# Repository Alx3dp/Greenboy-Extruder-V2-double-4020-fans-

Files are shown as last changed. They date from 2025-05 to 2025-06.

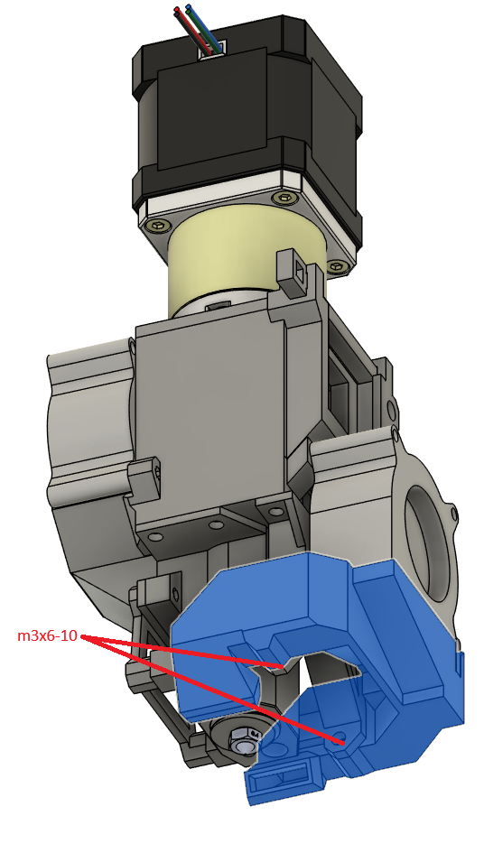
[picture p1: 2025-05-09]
Pellet printhead V2/assembly guide/step_9.png

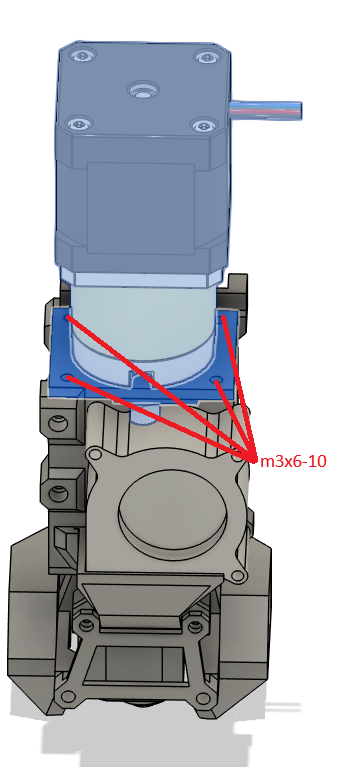
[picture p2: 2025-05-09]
Pellet printhead V2/assembly guide/step_11.png

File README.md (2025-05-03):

This is an alternate printhead for the Greenboy3d Pellet Extruder 
<br>
The goal of this project is to offer an alternate printhead to the original one with a multitude of improvements whith minimal extra parts needed over the kit the extruder comes with.
<br>
Notable improvements are:
<br>
<br>
A removable connector for the pellet hose including a gate to stop the pellet flow.
<br>
A significant improvement of the location of the center of mass(COM) of the printhead to hopefully allow faster printing
<br>
A mounting plate seperate of the main body which makes it significantly easier to create custom mounts and makes it possible to remove the printhead from the printer with minimal disassembly
<br>
Hopefully improved cooling
<br>
It is more compact than the original printhead
<br>
A dedicated mount for a multitude of z probes (still a wip)
<br>
There are also 2 versions, one with the pellet hose on the left and one with it on the right
<br>
<br>
Do keep in mind that this is still a wip. there can be issues, I can make mistakes and my designs are not perfect. If you find an issue or have any Ideas on how to improve this design please message me on discord @alx1234
<br>
You will need additional parts to the GB kit, consult the BOM to see what exactly you will need.
<br>
As the motor is by far the heaviest part of the printhead, the COM is located relatively high up. The closer the COM is to the x axis the better it is.
<br>
As a consequence of that the printhead has been moved down compared to the original, meaning you will lose a few centimeters of z travel.
<br>
<br>
The Fans I use as reference are a different model as the ones included with the GB kit, so they do not lign up with the fixtures in the .step files.
<br>
<br>
You need to ause support when printing these parts, I would recommend just using your standard tree support.
<br>
<br>
The main body of the printhead is in direct contact with the extruder barrel, so pla is most likely not sufficient for this part. So use something with better heat resistance like petg or abs at least for that part.

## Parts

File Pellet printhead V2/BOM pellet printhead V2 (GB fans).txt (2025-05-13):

The screw set included with the Greenboy pellet Extruder contains the 2 m3x25 and m3x18 screws that are needed for the fans,
as well as 12 m3x10 screws. 

So you need to source the rest of the screws yourself

Fans: 			2x m3x18			#for hotend cooling fan
			2x m3x18-25			#for part cooling fan

Motor mount:		4x m3x5x4 heat set insert	#located on top of the main body
			4x m3x8-12				#to secure the motor to the motor plate
			4x m3x6 to m3x10		#to secure the motor plate to the main body

Mounting plate:		4x m3x5x4 heat set insert	#for all Version, located on the side of the main body
			4x m3x6 to m3x10  		#for all Version
			4x m3x6				#for xol carriage
			2x m3x6 to m3x10		#for Ender 3
			2x m3x5 to m3x12		#for Neptune 3, the original Filament printhead uses 2 m3x8 for this 

hotend cooling duct:	2x m3x6 to m3x10		#to secure the fixture to the main Body
			
Z probe fixture:	4x m3x16 			#for cartographer probe
			2x m3x6				#for cartographer probe
			4x m3x10 to m3x12 		#for no probe

Part cooling duct:	2x m3x6 to m3x10		#to secure the fixture to the main Body,
			2x m3x6 to m3x10		#to secure the duct to the fixture

Extruder Barrel:	4 m4x8 to m4x12			#to secure the extruder barrel to the main body

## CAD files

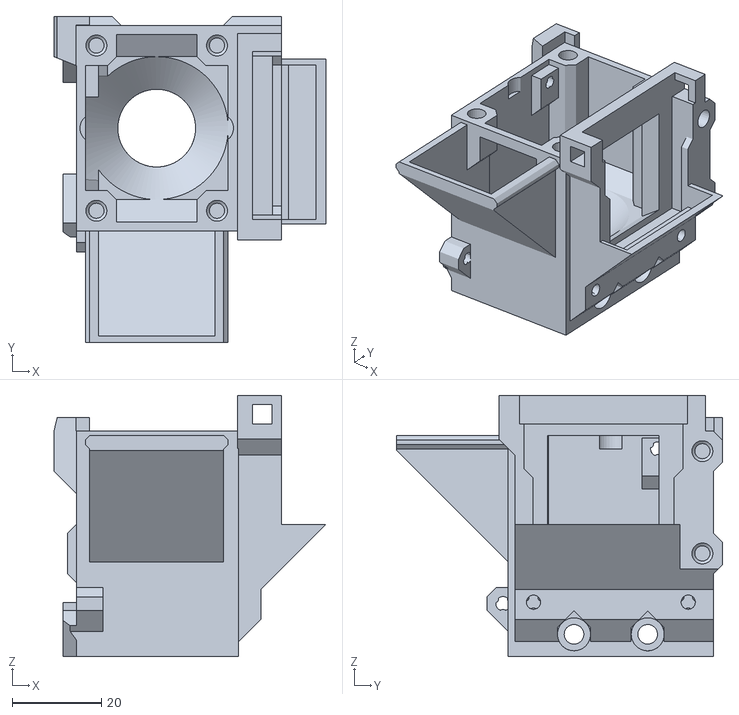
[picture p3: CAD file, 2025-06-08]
Pellet printhead V2/general/body designs/main body bucket.stl
60.9 x 73.0 x 58.5

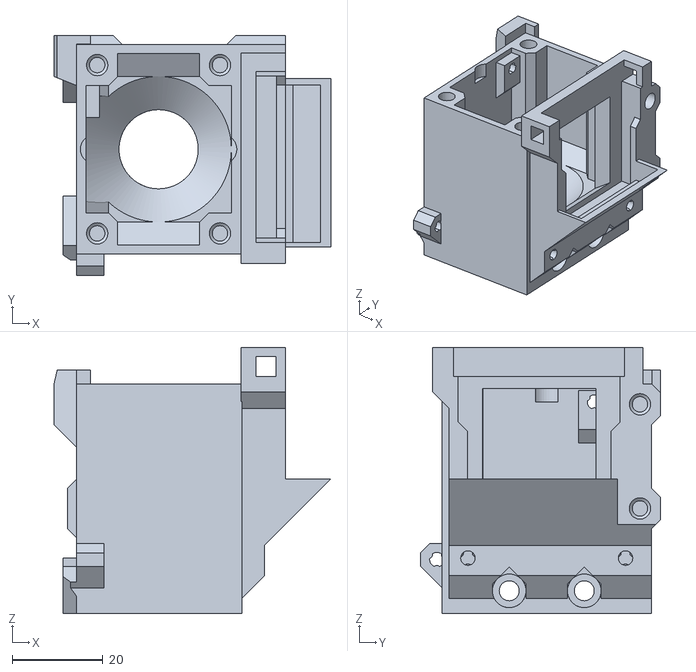
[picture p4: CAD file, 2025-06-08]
Pellet printhead V2/general/body designs/main body normal.stl
60.9 x 52.7 x 58.5

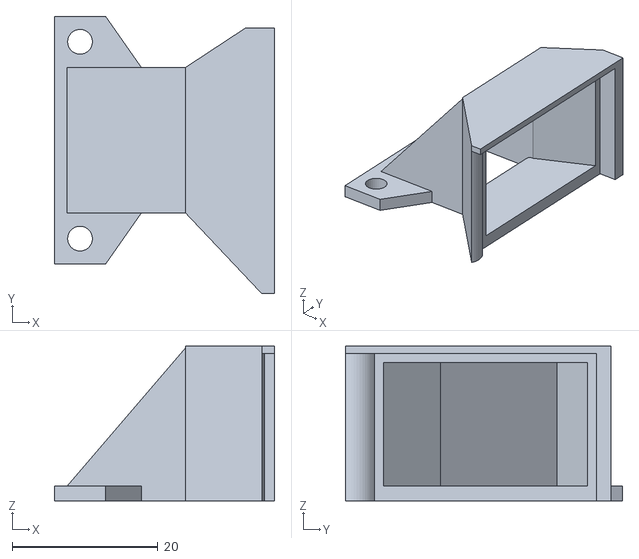
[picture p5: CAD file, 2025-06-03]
Pellet printhead V2/general/hotend fan duct.stl
30.2 x 38.1 x 21.2

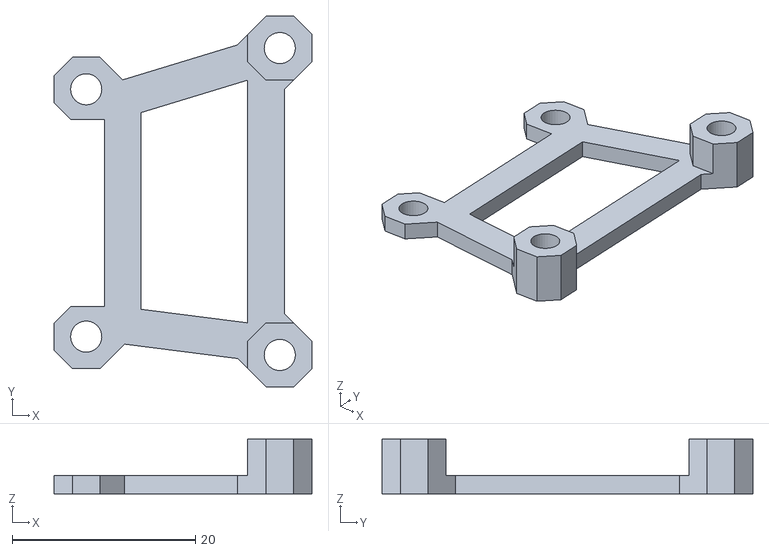
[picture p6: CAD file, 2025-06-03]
Pellet printhead V2/general/z probe adapters/no Z probe fixture.stl
28.1 x 40.5 x 6.00

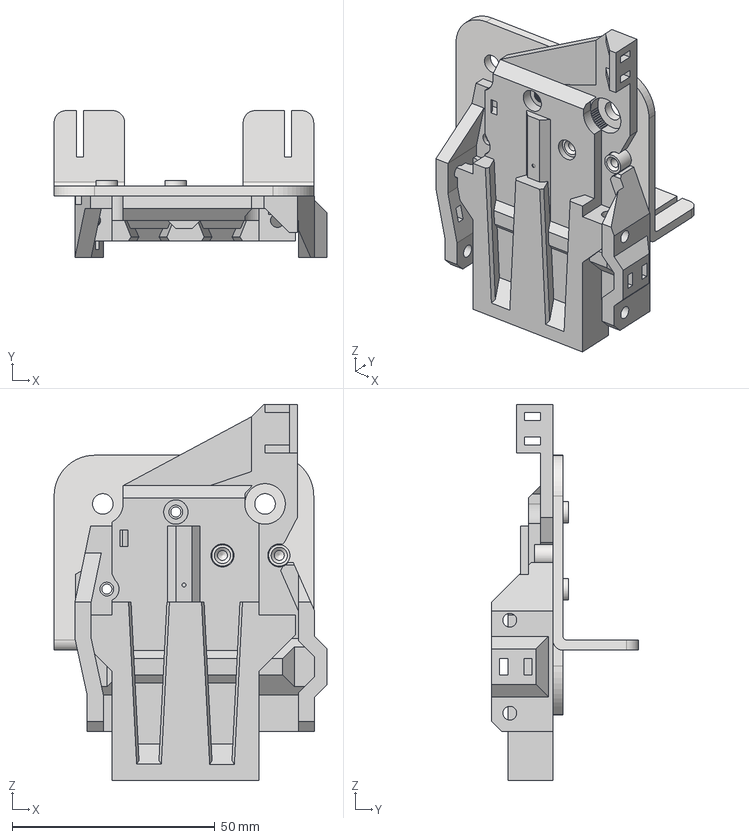
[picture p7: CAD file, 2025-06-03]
Pellet printhead V2/Mounting plates/Ender3/Ender3 pro mounting plate cad.step
67.2 x 36.2 x 92.7 mm
Основание_3
Pellet printhead V2 (GB parts) pellet hose right
Pellet printhead V2 (GB parts) pellet hose right_1

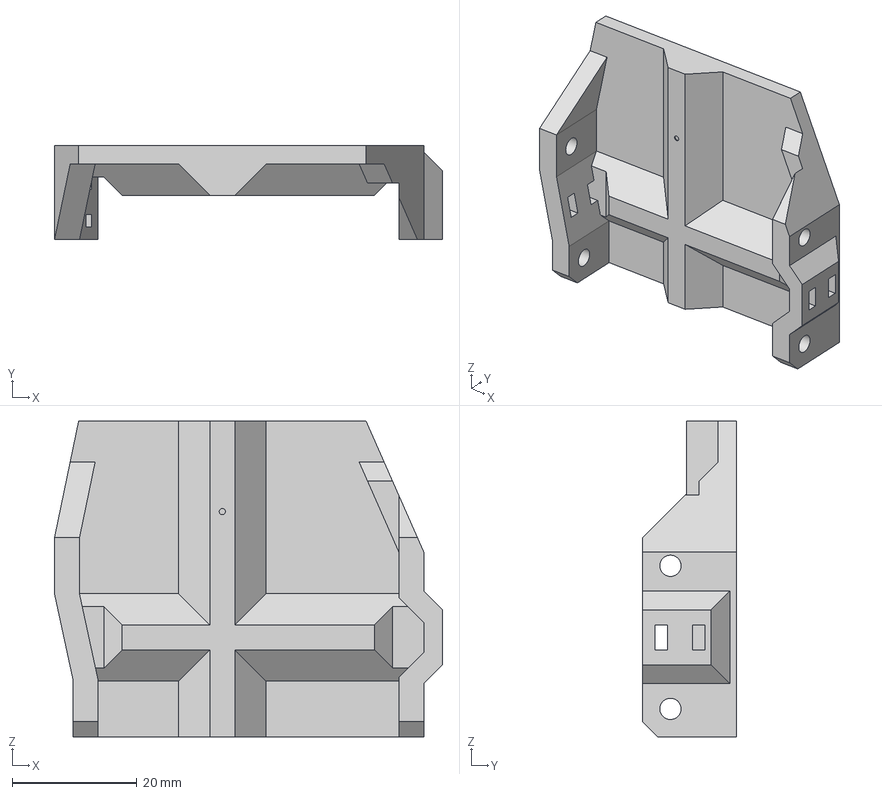
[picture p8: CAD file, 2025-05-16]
Pellet printhead V2/Mounting plates/mounting plate base hose right.step
62.1 x 15.1 x 50.6 mm

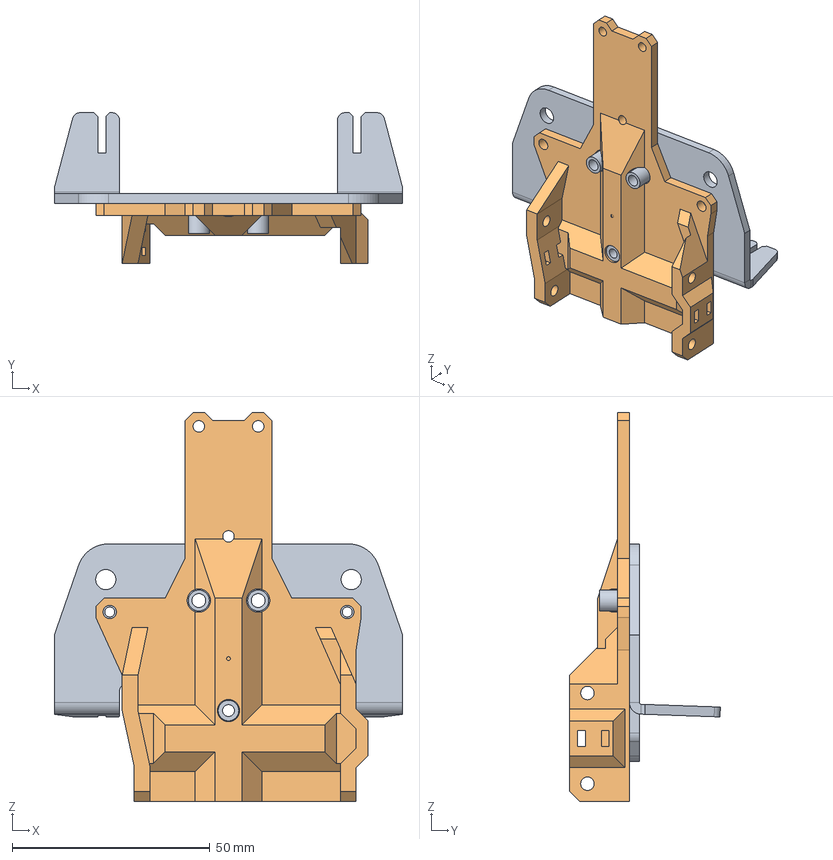
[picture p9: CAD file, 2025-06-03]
Pellet printhead V2/Mounting plates/Neptune 3/Neptune 3 Pro mounting plate cad.step
88.0 x 38.1 x 98.3 mm
FIXING_PLATE_EXTRUDER
Pellet printhead V2 (GB parts) pellet hose right

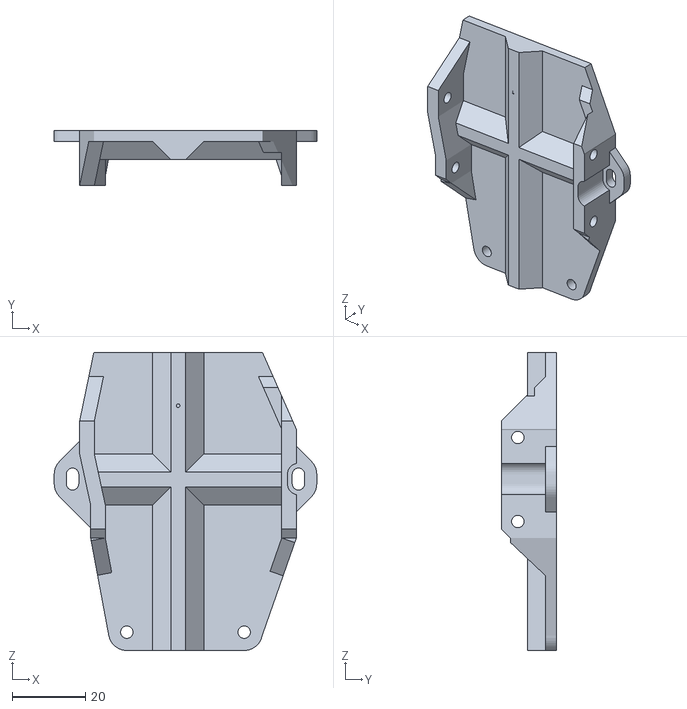
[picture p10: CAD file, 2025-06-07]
Pellet printhead V2/Mounting plates/Orange storm giga/orange storm giga mounting plate.stl
71.6 x 15.1 x 81.2

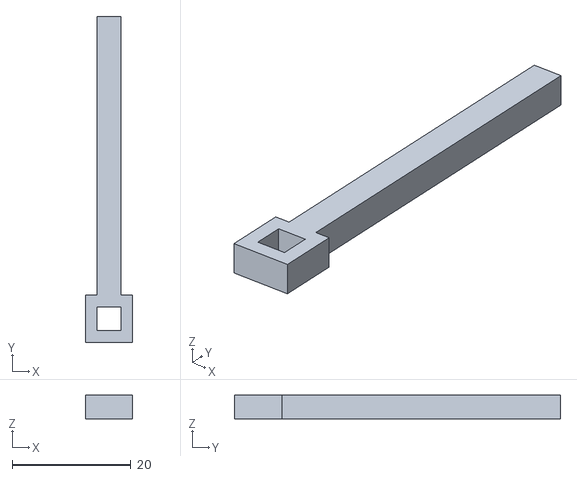
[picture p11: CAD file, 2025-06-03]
Pellet printhead V2/pellet hose connectors/top bar.stl
8.00 x 55.0 x 4.00

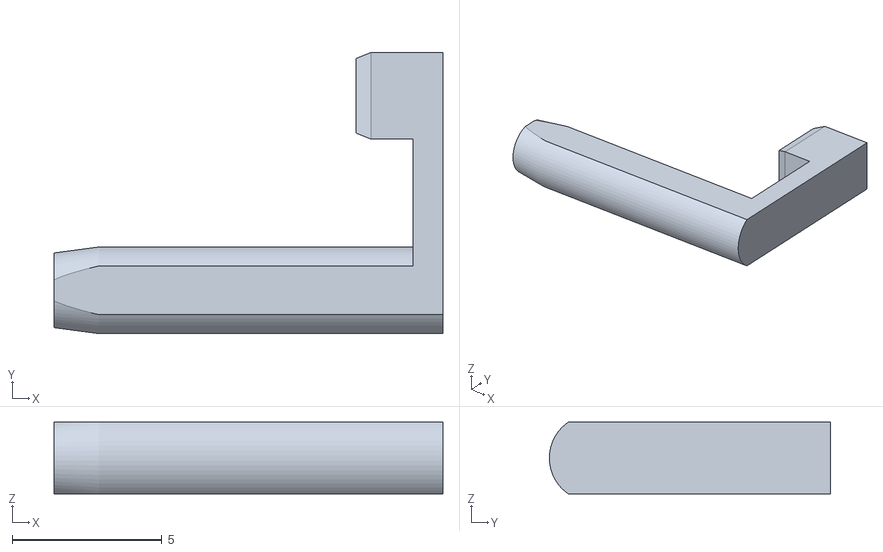
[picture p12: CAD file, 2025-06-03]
Pellet printhead V2/general/fan clip 1.stl
13.0 x 9.40 x 2.40

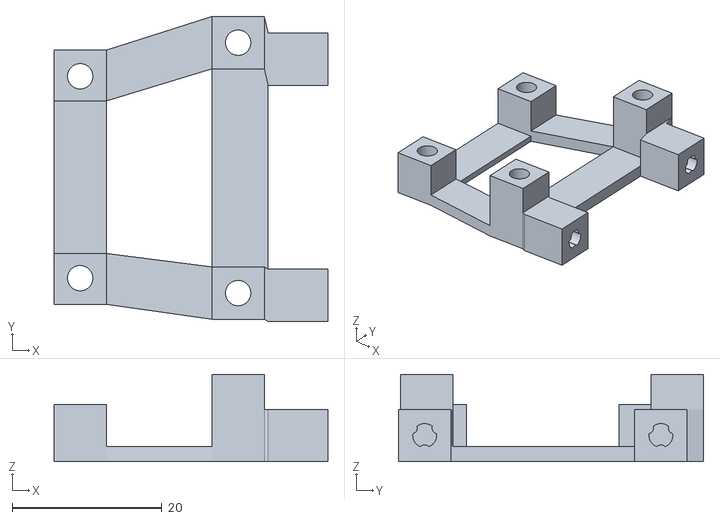
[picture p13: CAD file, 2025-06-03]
Pellet printhead V2/general/z probe adapters/cartographer probe fixture.stl
36.6 x 40.8 x 11.7

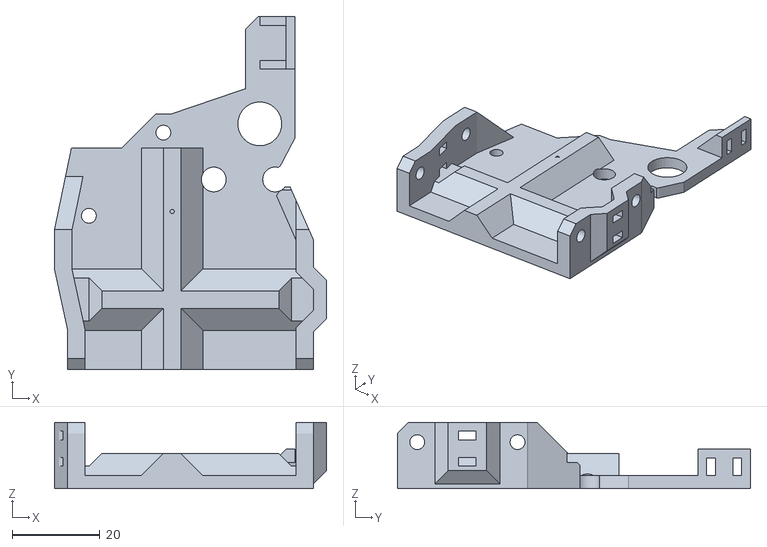
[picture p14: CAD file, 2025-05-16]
Pellet printhead V2/Mounting plates/Ender3/mounting plate hose right.stl
62.1 x 80.6 x 15.1

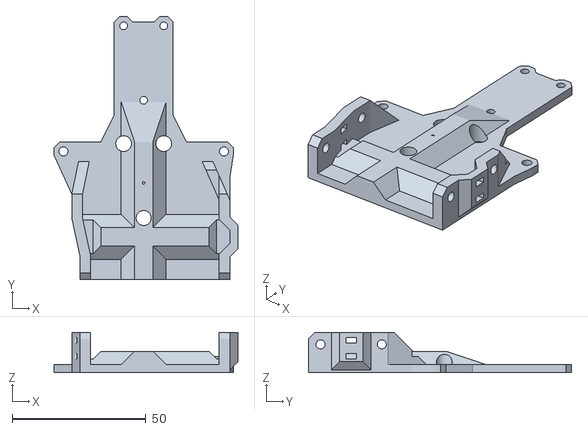
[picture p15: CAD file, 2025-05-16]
Pellet printhead V2/Mounting plates/Neptune 3/mounting plate hose right.stl
68.7 x 98.3 x 15.1

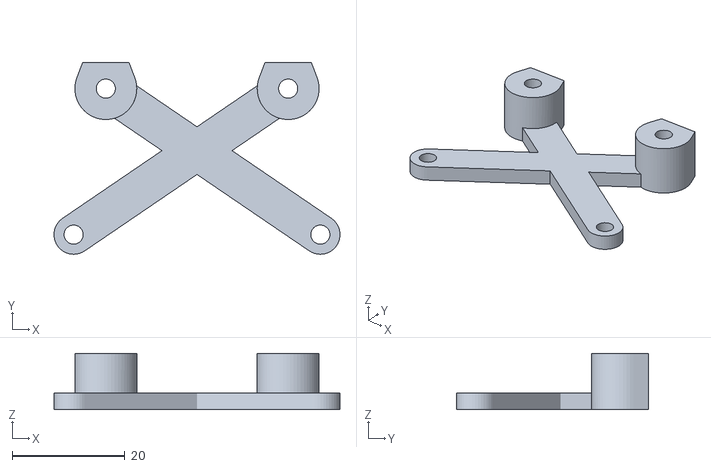
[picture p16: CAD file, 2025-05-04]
Pellet printhead V2/Mounting plates/XOL carriage/ebb36 fixture.stl
50.8 x 34.0 x 10.00

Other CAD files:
Pellet printhead V2/Mounting plates/XOL carriage/mounting plate hose right.stl
Pellet printhead V2/Mounting plates/Orange storm giga/orange storm giga mount.step
Pellet printhead V2/pellet hose connectors/pellet gate.stl
Pellet printhead V2/general/body designs/bucket lid.stl
Pellet printhead V2/Mounting plates/Ender3/Ender 3 z limit switch extension cad.step
Pellet printhead V2/Mounting plates/Ender3/z limit switch extension.stl
Pellet printhead V2/Mounting plates/XOL carriage/XOL carriage mounting plate cad.step
Pellet printhead V2/general/Hotend cooling duct.stl
Pellet printhead V2/general/extruder inlet guide.step
Pellet printhead V2/general/extruder inlet guide.stl
Pellet printhead V2/general/fan clip 2.stl
Pellet printhead V2/general/motor plate.stl
Pellet printhead V2/general/part cooling duct fixture.stl
Pellet printhead V2/general/part cooling duct.stl
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

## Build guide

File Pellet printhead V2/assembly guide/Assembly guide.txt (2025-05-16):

Alx3dp Greenboy Pellet Printhead V2 Assembly guide

Consult the BOM to see what screws you need for which parts

I also added simple pictures as reference for every given step

some pictures might be outdated but the concepts still apply

Step 0.1: You need to press 8 m3x5x4 heat set inserts into the main body, 
	4 on top for the motor mount and 
	2 on each sides in the back for the mounting plate
	You need to press these in with a soldering iron,
	I recommend using a bad tip or cleaning it right after of any plastic residue if it comes in contact with the plastic.
	The heatset inserts should be at least flush height wise and it is no issue if they are pushed in a bit more 
	I also recommend using tweezers or something similar to hold the insert in place when pulling the soldering iron out.

Step 0.2: you should assemble the hotend first before starting the assembly of the printhead. 
	-screw the nozzle into the extruder barrel
	-screw the heating block onto the extruder barrel
		The heating block should be roughly perpendicular to the screw holes in the barrel
	-insert the heater and thermistor into the proper holes and secure them with the grub screws 
	!be careful to not overtighten them!
	if you need to have the grub screws on the bottom to achieve the correct angle of the heating block and the thermistor is too short to reach the grub screw you can carefully remove a bit of insulation fom the thermistor, jsut be careful to not go past the protective metal sleeve 
	-the auger does not have to be inserted yet, jsut be sure to insert it before you mount the motor plate

Step 1: press the hose connector onto the hose adapter 

Step 2: mount the motor plate onto te motor using 4 m3x6-10 screws. 
	At this point you should decide in which direction you want the motor cables to go.
	I would not recommend having the cables on the seide where the pellet hose connector is, as this makes 

Step 3: push the extruder barrel into the main  body and secure it with the 4 m4 screws.
	The m4 scres can be 8-12mm in length
	make sure that the heating block is turned to the back

Step 4: Mount the Hotend cooling duct onto the main body with 2 m3x6-10 screws
	the older version uses 4 screws for this

Step 5: Mount the the part cooling duct fixture onto the main body with 2 m3x6-10 screws
	You need to access the screws at a angle, so use the ball-end of the allen key

Step 6: mount the hotend fan duct and your chosen z probe fixture with 4 screws, 
	the exact screw lengths are referenced in the BOM under "z probe fixture"

Step 7: Mount the Hotend fan with 2 m3x18 screws to the main body

Step 8: Mount the part cooling fan to the part cooling duct with the 2 printed clips

Step 9: Mount the part cooling duct with the part cooling fan to the part cooling duct fixture using 2 m3x6-10 screws

Step 10: Secure the part cooling fan to the main body with 2 m3x18-25 screws

Step 11: Put the coupler on the shaft of the pellet screw.  
	Afterwards mount the motor with the motor plate to the main body with 4 m3x6-10 screws

Step 12: Tighten the screws on the coupler through the hole for the pellet hose to secure the screw to the motor shaft
	Make sure the pellet screw is seated as far down as possible and not lifted out of the barrel

Step 13: Slide the pellet hose adapter into its slot from the top, afterwards secure it with the top bar

Step 14: Mount the Mounting plate on your printer, the exact screws needed for this depends on 	your printer 
	Consult the BOM under "Mounting plate" to find what exactly you need for your version

Step 15: Mount the Printhead onto the Mounting plate with 4 m3x6-10 screws

Step 16: Screw the pellet hose into the Pellet hose adapter

After this you should be done. If anything is missing or there are any issues with this guide please dm or @ me in the Greenboy3D discord @alx1234

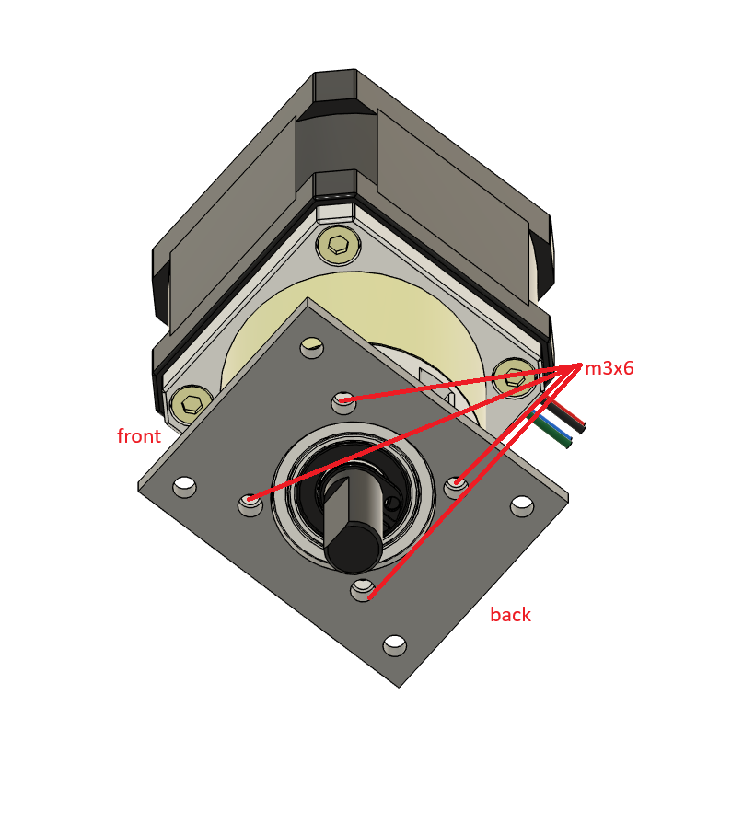
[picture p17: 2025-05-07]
Pellet printhead V2/assembly guide/step_2.png

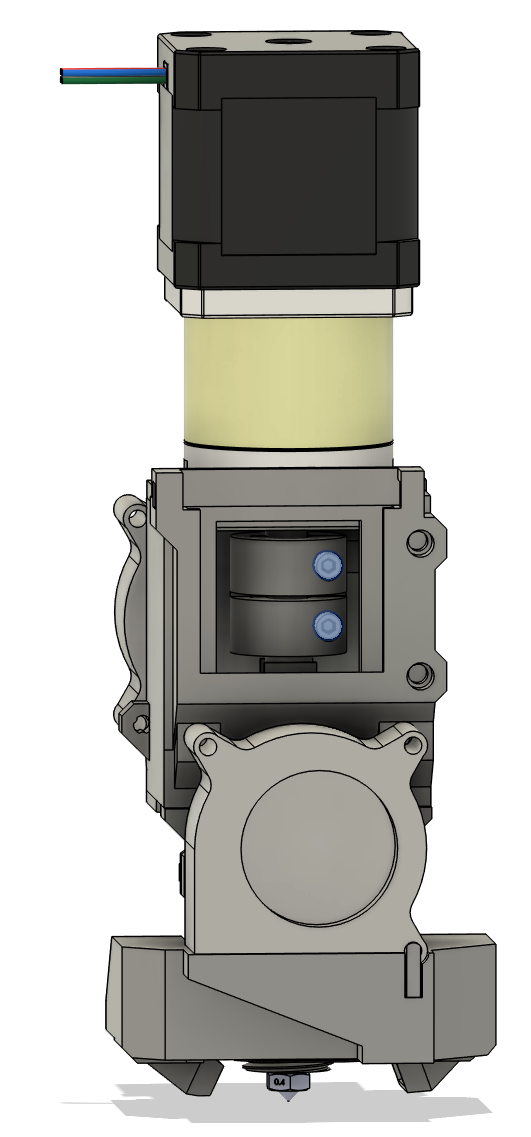
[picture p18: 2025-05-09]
Pellet printhead V2/assembly guide/step_12.png

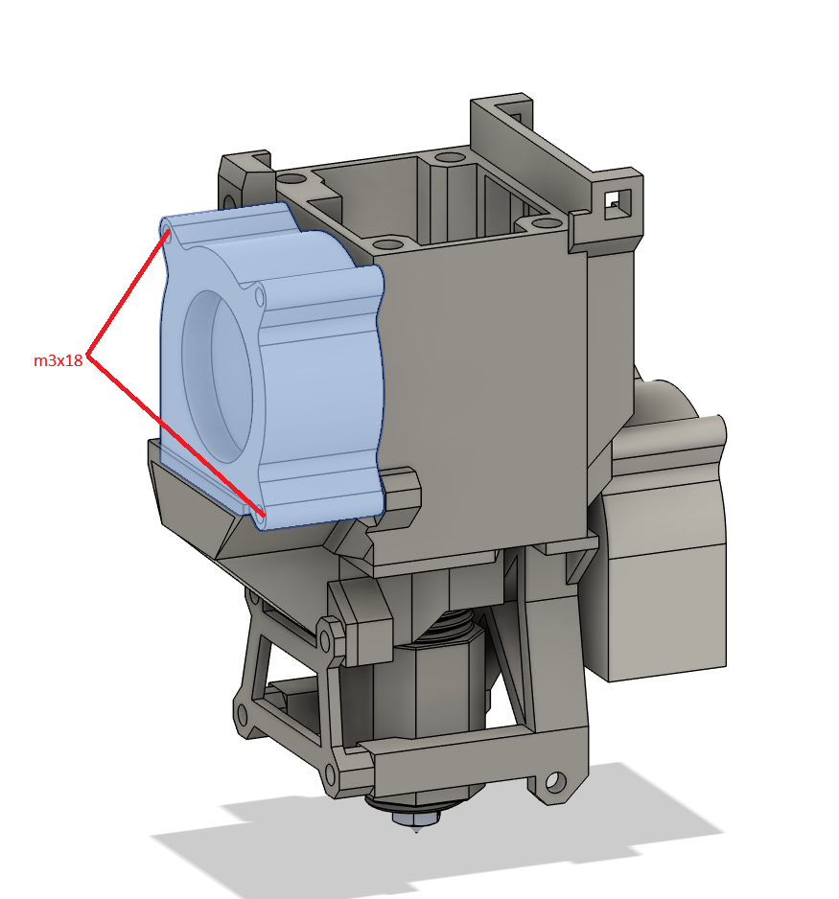
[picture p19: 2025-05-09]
Pellet printhead V2/assembly guide/step_7.png

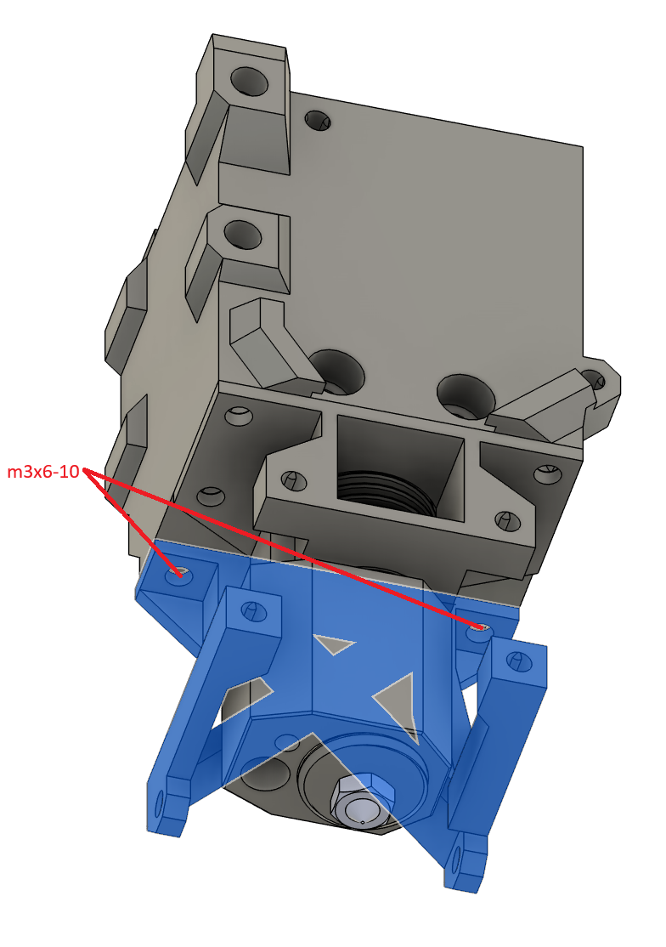
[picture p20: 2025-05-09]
Pellet printhead V2/assembly guide/step_5.png
